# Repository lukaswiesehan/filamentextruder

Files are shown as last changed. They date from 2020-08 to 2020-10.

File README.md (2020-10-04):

# Filament-Extruder <!-- omit in toc -->

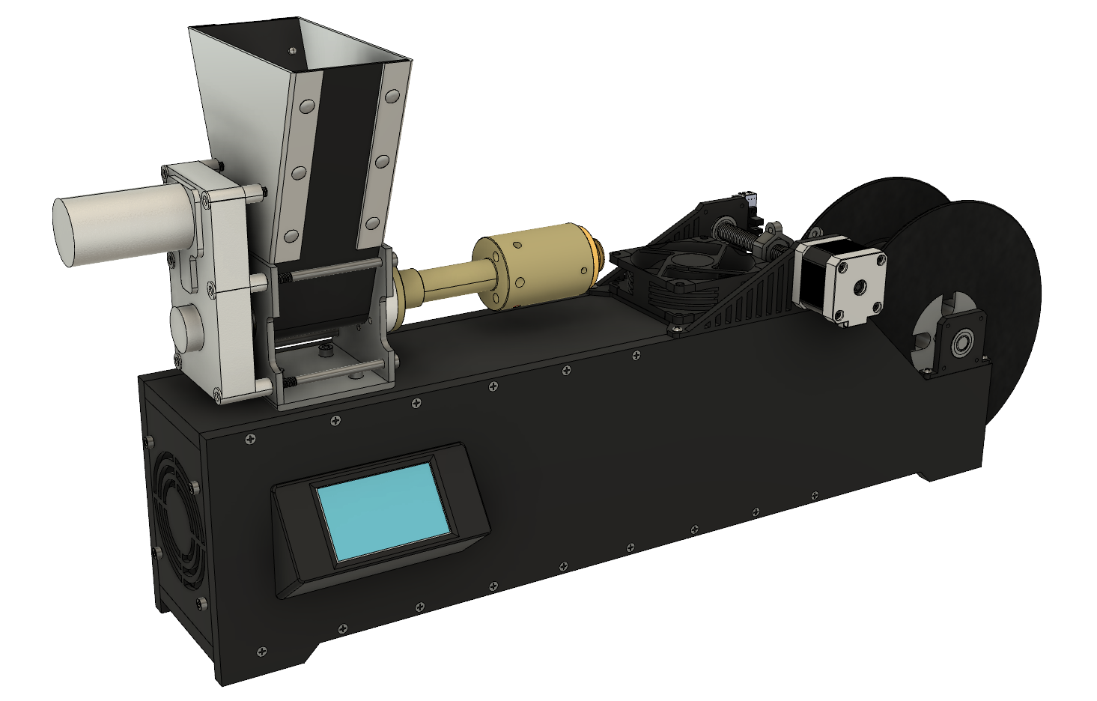
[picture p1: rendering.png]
HMI Preview


Bachelorprojekt im Studiengang Mechatronik, HAW Hamburg.  
*Entwickelt von Tobias Freytag, Anton Neike, Max Sahlke, Lukas Wiesehan.  
Betreut von Prof. Dr. Dietmar Pähler.*

###### Inhalt <!-- omit in toc -->
- [Einführung](#einführung)
- [Repo-Struktur](#repo-struktur)
- [Hardware](#hardware)
  - [Bestellliste](#bestellliste)
  - [Verdrahtung des Systems](#verdrahtung-des-systems)
    - [Arduino Mega](#arduino-mega)
    - [Arduino Nano](#arduino-nano)
    - [Mosfet-Module](#mosfet-module)
    - [Heizpatronen](#heizpatronen)
    - [PT100 Signalverstärker](#pt100-signalverstärker)
    - [PT100 Temperatursensor](#pt100-temperatursensor)
    - [Relais-Modul](#relais-modul)
    - [Extruder Motor](#extruder-motor)
    - [Filament-Lüfter](#filament-lüfter)
    - [Schrittmotortreiber](#schrittmotortreiber)
    - [Schrittmotoren](#schrittmotoren)
    - [Optischer Endschalter](#optischer-endschalter)
- [Software](#software)
- [Konfiguration des Systems](#konfiguration-des-systems)
- [Bedienung des Systems](#bedienung-des-systems)

## Einführung

Im Rahmen des Bachelorprojekts im 5. Semester des Bachelorstudiengangs Mechatronik an der HAW Hamburg soll eine Anlage konstruiert und realisiert werden, 
die aus Kunststoffgranulat 3D-Druck Filament extrudiert und dieses auf entsprechende Rollen aufspult. Übergeordnetes Ziel ist es, Prototypen oder 
fehlgeschlagene Druckteile zu schreddern, um sie erneut zu Filament zu extrudieren und dieses erneut zu verwenden. Da sowohl die Qualität des Kunststoffs, als
auch die Verarbeitbarkeit unter häufigem Aufschmelzen leiden, soll das mit der Anlage hergestellte Filament lediglich für den Druck von Prototypen verwendet
werden.

###### Funktionsschema <!-- omit in toc -->
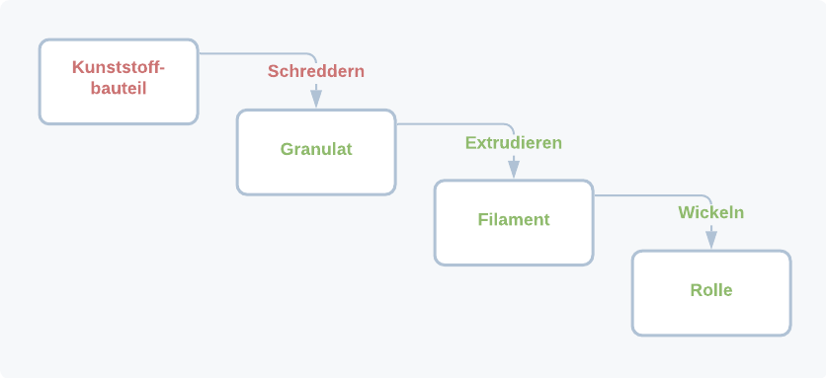
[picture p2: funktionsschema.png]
Funktionsschema


Die im Funktionsschema grün dargestellten Elemente sind Teil dieses Projekts. Die Konstruktion eines Schredders ist im Rahmen dieses Projekts nicht möglich, allerdings
kann das System in Folgeprojekten durchaus mit einem Schredder erweitert werden, der auf den Trichter des Extruders aufgesetzt werden sollte.

## Repo-Struktur

Das Stammverzeichnis des Repositorys beinhaltet alles, was für eine Rekonstruktion des Systems notwendig ist. Es teilt sich in folgende Unterverzeichnisse auf.

| Verzeichnis | Inhalt |
|---|---|
| [`/arduino`](/arduino) | Arduino-Projekte, Liste der notwendigen Libraries, Anleitung zur notwendigen Modifikation der Nextion-Library |
| [`/cad`](/cad) | CAD-Modell des fertigen Systems, `.stl`-Dateien der gedruckten Einzelteile |
| [`/hmi`](/hmi) | `.HMI`-Datei und Anleitung zur Installation des Interfaces auf dem Nextion Display, Screenshots des Interfaces |

Die hier abgelegten Daten entsprechen dem finalen Entwicklungsstand des Systems. Die **ausführliche Projektdokumentation**, in der die einzelnen Entwicklungsschritte 
während des Projekts näher ausgeführt sind, ist als [Wiki dieses Repos](https://github.com/lukaswiesehan/filamentextruder/wiki) realisiert.

## Hardware

Nachfolgend werden alle Komponenten aufgelistet, die bestellt werden müssen. Gehäuse- und Druckteile sind in [`/cad`](/cad) abgelegt und können auf unterschiedliche Weise gefertigt 
werden, weshalb sie in der Kostenaufstellung nicht berücksichtigt werden. Zudem werden Kabel zur Verdrahtung des Systems benötigt, die hier ebenfalls nicht aufgelistet sind.

### Bestellliste

| Anzahl | Bezeichnung | Beschreibung | Preis |
|:---:| --- | --- |:---:|
| 1x | [Felfil Evo Basic Kit](https://felfil.com/shop/felfil-evo-basic-kit/?v=5ea34fa833a1) | Basiskomponenten des Extruders als Bausatz | 299,00€ |
| 1x | [Kaltgerätebuchse](https://www.amazon.de/Hifi-Lab-Einbau-Stecker-Einbau-Buchse-Kaltger%C3%A4te-Buchse/dp/B01H5MK3OI) | Spannungsversorgung des Systems | 6,39€ |
| 1x | [Kaltegeräte-Anschlusskabel](https://www.conrad.de/de/p/hawa-1008230-kaltgeraete-anschlusskabel-schwarz-2-00-m-621535.html) | Spannungsversorgung des Systems | 4,86€ |
| 1x | [Netzteil 24V 320W](https://www.conrad.de/de/p/mean-well-rsp-320-24-ac-dc-netzteilbaustein-geschlossen-13-4-a-321-6-w-24-v-dc-1293056.html) | Primäre Spannungsquelle des Systems | 62,38€ |
| 1x | [Spannungswandler XL4016](https://www.az-delivery.de/products/xl4016-step-down-buck-converter-dc-dc?_pos=5&_sid=a325961b4&_ss=r) | Spannungsversorgung der 12V-Komponenten (Extrudermotor & Lüfter) | 8,49€ |
| 1x | [Spannungswandler LM2596S](https://www.az-delivery.de/products/lm2596s-dc-dc-step-down-modul-1?_pos=6&_sid=619fecdd6&_ss=r) | Spannungsversorgung der 5V-Komponenten (Display & Arduino) | 5,29€ |
| 1x | [Arduino Mega](https://www.az-delivery.de/products/mega-2560-r3-board-mit-atmega2560-100-arduino-kompatibel-ohne-usb-kabel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) | Steuerung des Extruder-Systems und des HMI | 13,79€ |
| 1x | [Arduino Nano](https://www.az-delivery.de/products/nano-v3-mit-ch340-arduino-kompatibel) | Steuerung des Wicklungsmechanismus | 6,49€ |
| 1x | [Nextion Display NX4024K032](https://www.amazon.de/MakerHawk-Nextion-NX4024K032-erweiterte-Versionen/dp/B072FN3SFH/) | Anzeige und Touch-Interface zur Steuerung des Systems | 38,44€ |
| 3x | [Mosfet Modul IRF520](https://www.az-delivery.de/products/irf520-mos-driver-modul-0-24v-5a?_pos=1&_sid=0db666f69&_ss=r) | Steuerung der Heizpatronen | 4,29€ |
| 3x | [Heizpatrone 24V](https://www.conrad.de/de/p/24v-40w-heizpatrone-j-head-hotend-heater-cartridge-3d-drucker-802287254.html) | Heizmodule des Extruders | 4,50€ |
| 1x | [Temperatursensor PT100](https://www.conrad.de/de/p/heraeus-nexensos-w-eyk-6-pt100-platin-temperatursensor-40-bis-500-c-100-3850-ppm-k-172412.html) | Sensor zur Bestimmung der Extrudertemperatur | 15,03€ |
| 1x | [Adafruit MAX31865](https://www.conrad.de/de/p/adafruit-pt1000-rtd-temperature-sensor-amplifier-max31865-802235187.html) | Modul zur Wandlung des Sensorsignals des PT100 | 19,33€ |
| 2x | [Schrittmotortreiber SMD356C](https://www.conrad.de/de/p/waveshare-smd356c-three-phase-hybrid-stepper-motor-driver-806805951.html) | Steuerung der Wicklungsmotoren | 41,44€ |
| 2x | [Schrittmotor NEMA-17](https://www.conrad.de/de/p/joy-it-schrittmotor-nema-17-01-nema-17-01-0-4-nm-1-68-a-wellen-durchmesser-5-mm-1597325.html) | Antriebe des Wicklungsmechanismus | 27,20€ |
| 1x | [Optischer Endschalter](https://www.amazon.de/Homyl-Optischer-Begrenzungsschalter-Endanschlag-Werkzeuge-Rot/dp/B07MHFTVNF/) | Referenzierung des Führungsmotors | 2,51€ |
| 1x | [Relais-Modul KY-019](https://www.az-delivery.de/products/relais-modul) | Schalten des Extrudermotors | 4,99€ |
| 2x | [PC-Lüfter 80x80x25](https://www.conrad.de/de/p/logilink-fan101-pc-gehaeuse-luefter-schwarz-b-x-h-x-t-80-x-80-x-25-mm-871001.html) | Kühlung elektronischer Bauteile und des Filaments | 4,18€ |

Die Kosten der elektronischen Bauteile summieren sich damit auf **659,00€** zzgl. diverser Versandkosten sowie der Gehäuse- bzw. Druckteile.
Hierzu zählen Holzschrauben, einige M4- und M5-Schrauben und Muttern, `10 mm` Sperrholz, `2 mm` Aluminiumblech, sowie etwa `250 mm` M12-Gewindestange.

### Verdrahtung des Systems

###### Verdrahtung <!-- omit in toc -->
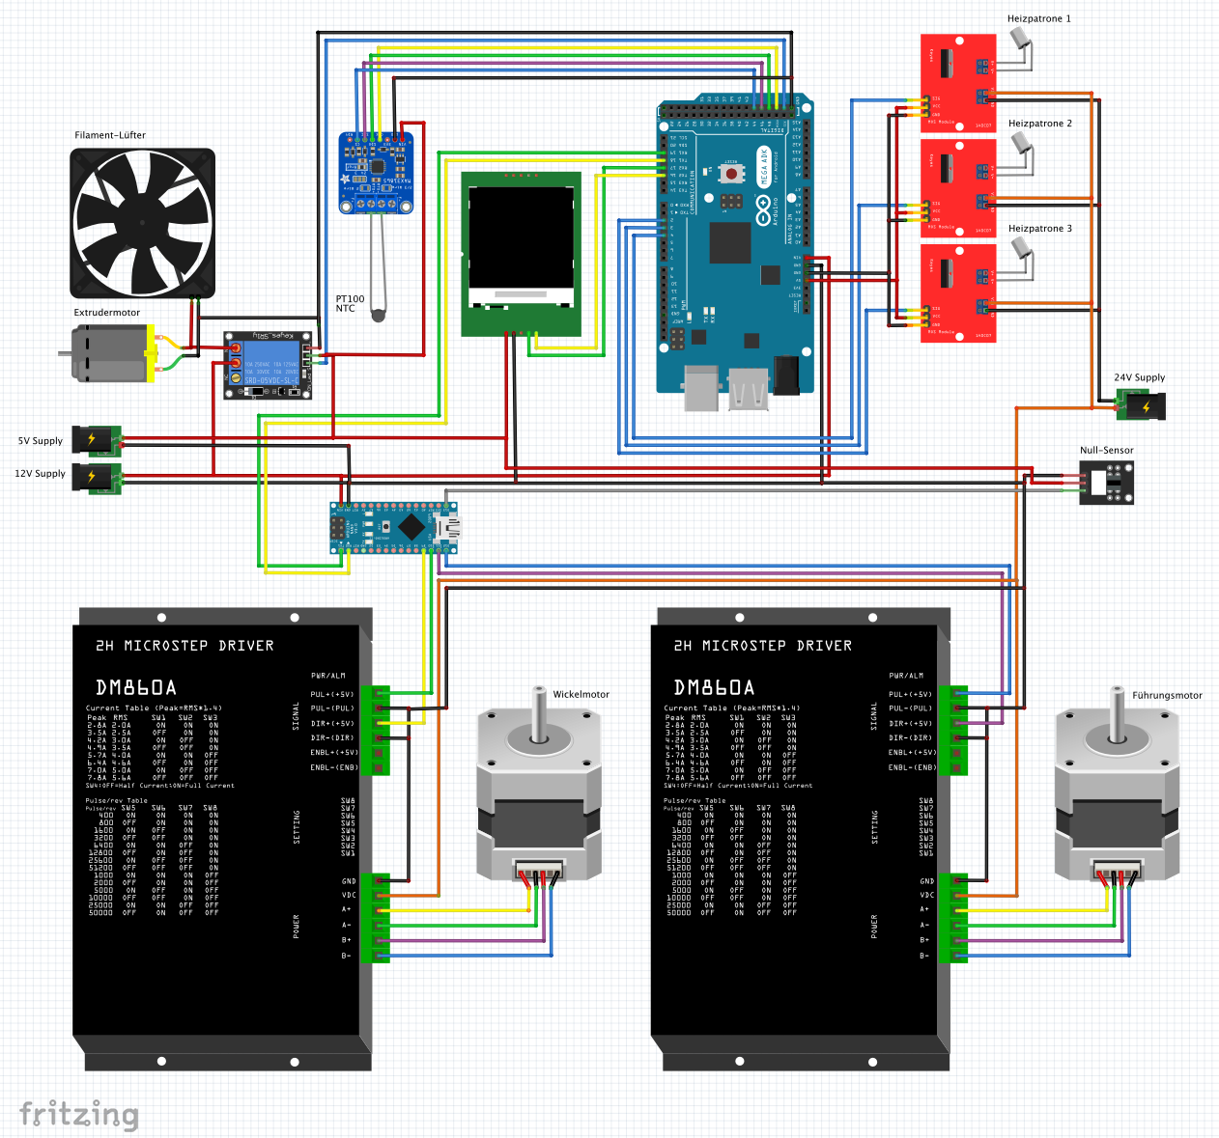
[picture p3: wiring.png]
Verdrahtung


Im oben abgebildeten Schema wurde folgende Farbkonvention eingehalten:
- Schwarz: GND
- Rot: 5-12V VCC
- Orange: 24V VCC
- Blau, Grün, Gelb, Lila: Daten/Signale

*Hinweis: Das Nextion Display wurde im Schema durch ein ähnliches Display ersetzt,
welches sich sowohl im Maßstab, als auch in der Pin-Belegung unterscheidet.*

*Hinweis: Es ist darauf zu achten, dass alle Elemente des Systems auf das selbe `GND`-Niveau gelegt sind.*

#### Arduino Mega

Der Arduino Mega dient als primärer Prozessor des Systems, auf dem die Temperaturregelung
und die Displaysteuerung implementiert sind. Er wird an `GND` und `12 V` Versorgungsspannung angeschlossen.

#### Arduino Nano

Der Arduino Nano wird für die Steuerung des Wicklungsmechanismus benötigt, da die Ansteuerung
der Schrittmotoren eine Signalfrequenz benötigt, die auf dem Mega wegen der darauf laufenden 
Temperaturregelung nicht gewährleistet werden kann. Der Nano wird zur Versorgung ebenfalls
an `GND` und `12 V` angeschlossen. Zudem wird der Hardware-Serial des Nanos mit den Pins `TX`
und `RX` an `RX1` und `TX1` des Mega, also dessen Hardware-Serial 1 verbunden, sodass eine
Kommunikation zwischen den beiden Arduinos implementiert werden kann.

#### Mosfet-Module

Die drei Mosfet-Module werden jeweils `GND` und `24 V` Versorgungsspannung angeschlossen.
Für die Ansteuerung werden `GND` und `VCC` mit dem `5 V` Ausgang und `SIG` mit je einem 
PWM-Ausgang (hier Pins `1`, `2` und `3`) des Arduino Mega verbunden. 

#### Heizpatronen

Die Heizpatronen werden jeweils an die beiden Ausgangs-Terminals der Mosfet-Module angeschlossen. Die Polarität spielt hierbei keine Rolle.

#### PT100 Signalverstärker

Das Adafruit-Modul MAX31865 zum Auslesen des PT100-Sensors wird an `GND` und `5 V` Versogungsspannung angeschlossen. Zur Übertragung der Temperatur an den Arduino Mega werden
die Pins `CS`, `DI`, `DO` und `CLK` an vier Digital-Pins (hier Pins `45`, `47`, `49` und `51`) des Mega angeschlossen.

#### PT100 Temperatursensor

Der PT100 Sensor wird an das Sensorterminal des Adafruit MAX31865 angeschlossen. Da es sich
um einen PT100 mit zwei Kabeln handelt, werden die mittleren beiden Anschlüsse des Moduls
verwendet.

Zur Verwendung des Moduls und des PT100 in Kombination mit einer entsprechenden
Arduino-Library findet sich auf der [Adafruit-Website](https://learn.adafruit.com/adafruit-max31865-rtd-pt100-amplifier/arduino-code) ein umfangreiches Tutorial.

#### Relais-Modul

Das Relais-Modul KY-019 soll zur Steuerung des Extruder-Motors verwendet werden, weshalb an 
den `COM`-Port `12 V` Versorgungsspannung angelegt wird. An der Signalseite wird das Modul
mit `GND` und `5 V` versorgt. Der `SIG`-Pin wird an einen Digitalpin (hier Pin `53`) des Arduino Mega angeschlossen. 

#### Extruder Motor

Der Extruder-Motor wird am Negativ-Pol mit `GND` verbunden, während der Positiv-Pol auf den
`NO`-, also "Normally Open"-Ausgang des Relais-Moduls gelegt wird.

#### Filament-Lüfter

Da der Lüfter zur Kühlung des Filaments nur benötigt wird, sofern extrudiert wird, wird er
analog zum Extruder-Motor mit `GND` versorgt und mit dem Positiv-Pol an das `NO`-Terminal
des Relais-Moduls angeschlossen.

#### Schrittmotortreiber

Die Schrittmotortreiber werden jeweils mit `GND` und `24 V` versorgt. Die `GND`-Leitung kann zudem jeweils direkt mit auf `PUL-` und `DIR-` der Signalterminals gelegt werden. `PUL+` und
`DIR+` werden an jeweils einen Digitalpin des Arduino Nano angeschlossen. Der Wicklungsmotor
ist hier an `10` und `9`, der Führungsmotor an `12` und `11` angeschlossen.

*Wichtig: die Schrittmotortreiber müssen mit den 6 Schaltern auf folgende Konfiguration eingestellt werden.*

| S1 | S2 | S3 | S4 | S5 | S6 |
|:-:|:-:|:-:|:-:|:-:|:-:|
| 0 | 0 | 0 | 1 | 1 | 0 |

#### Schrittmotoren

Die Schrittmotoren werden jeweils an `A-`, `A+`, `B-` und `B+` der Motortreiber angeschlossen. Die genaue Belegung kann vom Schrittmotor abhängig sein, daher wird an 
dieser Stelle auf [dieses Tutorial](https://www.makerguides.com/tb6600-stepper-motor-driver-arduino-tutorial/) verwiesen, in dem beschrieben wird, wie die
die korrekte Belegung der Schrittmotoren bestimmt werden kann.

#### Optischer Endschalter

Der optische Endschalter wird an `GND` und `5 V` Versorgungsspannung angeschlossen und mit
dem `S`- bzw. Signal-Pin auf einen Digitalpin (hier Pin `13`) des Arduino Nano gelegt.

## Software

Die Software besteht aus zwei Komponenten, die sich im Ordner [`/arduino`](/arduino) befinden.
Die genauen Funktionsweisen der Codes können den zugehörigen README-Dateien entnommen werden. 
Wie im Bereich *Hardware* bereits angedeutet, wird das Arduino-Projekt [`filamentextruder`](/arduino/filamentextruder) auf den Arduino Mega und das Projekt [`motorsteuerung`](/arduino/motorsteuerung) auf den Arduino Nano hochgeladen.

Weiterhin muss die Display-Software auf das Nextion-Display geladen werden. Eine kurze Beschreibung dessen findet
sich im Verzeichnis [`/hmi`](/hmi).

## Konfiguration des Systems

Um einen optimalen Prozess zu gewährleisten, sollten vor Inbetriebnahme einige Dinge beachtet werden.

Je nach thermischer Isolation des Extruders werden sich die Reglerparameter ein wenig unterscheiden. Da das System verhältnismäßig träge ist,
stellt das kein großes Problem dar. Um den Aufheizvorgang dennoch hinsichtlich seiner Dauer und Genauigkeit zu optimieren, sollten die PID-Parameter
dem System entsprechend eingestellt werden. Wie dazu vorgegangen werden sollte, kann dem Wiki-Kapitel [Entwicklung/Temperaturregelung](https://github.com/lukaswiesehan/filamentextruder/wiki/Entwicklung#temperaturregelung) entnommen werden. Die bestimmten Reglerparameter können dann in [`filamentextruder.ino`](/arduino/filamentextruder/filamentextruder.ino#L40) aktualisiert werden.

Weiterhin sollte die Basis-Geschwindigkeit der Wicklung an den Extruder angepasst werden, obwohl sie durch die Verwendung des selben mitgelieferten Motors
nur unwesentlich unterscheiden sollte. Im Wiki-Kapitel [Entwicklung/Wicklungsmechanismus](https://github.com/lukaswiesehan/filamentextruder/wiki/Entwicklung#wicklungsmechanismus)
wird ausführlich beschrieben, wie der Parameter `EXTRUSION_FEED` an das System angepasst werden sollte, um einen optimalen Filamentdurchmesser nach der Extrusion
zu gewährleisten. Dieser Parameter wird anschließend in [`motorsteuerung.ino`](/arduino/motorsteuerung/motorsteuerung.ino#L11) aktualisiert.

## Bedienung des Systems

###### Extruder im Prozess <!-- omit in toc -->
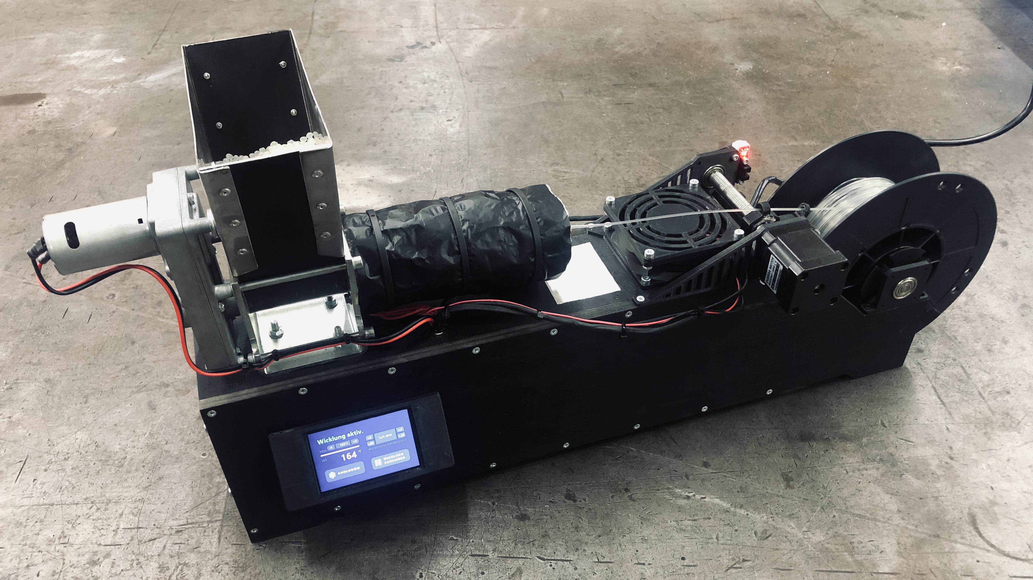
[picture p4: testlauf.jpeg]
Testlauf


Die Benutzeroberfläche wurde mit einer einfachen Bedienbarkeit im Hinterkopf designed. Der Bediener wird im Wesentlichen durch die Seiten geleitet, 
die den verschiedenen States des [Zustandsautomaten](/arduino/filamentextruder#finite-state-machine) entsprechen. Der Ablauf der Bedienung, die 
demnach streng an den Prozess gebunden ist, ist im Folgenden kurz beschrieben.

| Pos. | Beschreibung | Abbildung |
| :-: | --- | --- |
| **1.** | Einschalten der Anlage am Schalter der Kaltgerätebuchse | |
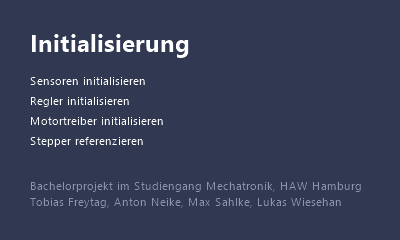
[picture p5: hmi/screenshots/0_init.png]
Initialisierung
| **2.** | Warten, bis das System initialisiert und der Führungsmotor referenziert ist. |  |
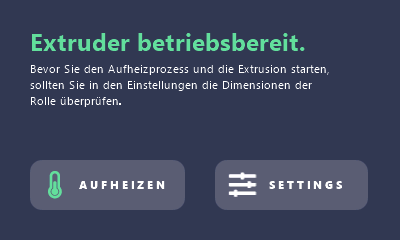
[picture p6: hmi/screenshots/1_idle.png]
Idle
| **3.** | Im Idle-Zustand kann der Bediener entweder den Prozess starten oder die Einstellungen öffnen. |  |
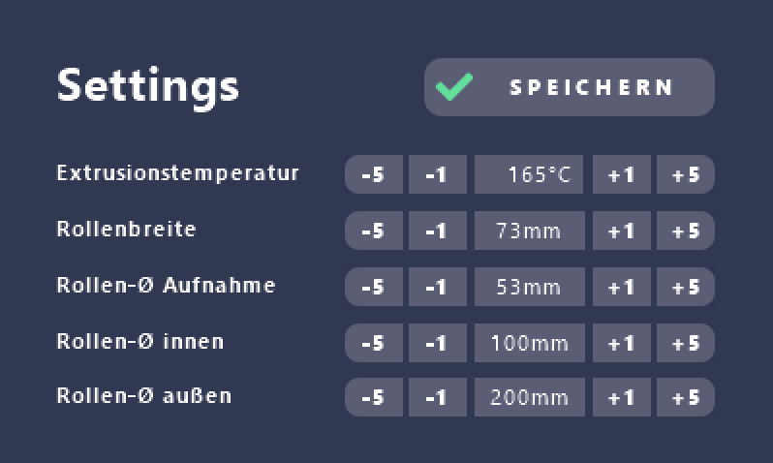
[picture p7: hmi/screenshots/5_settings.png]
Settings
| **3a.** | In den Einstellungen kann die Größe der Spule eingestellt werden, die für den Wicklungsprozess benötigt wird. Außerdem kann die Extrusionstemperatur an den verwendeten Kunststoff angepasst werden. |  |
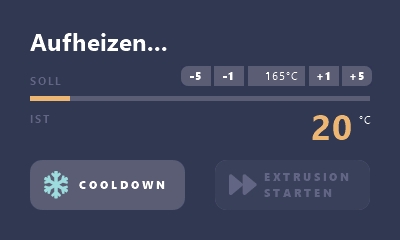
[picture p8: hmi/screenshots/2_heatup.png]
Heatup
| **3b.** | Wählt der Bediener in **3.** den Punkt aufheiten, so wird der Prozess gestartet. Warten, bis die Extrusionstemperatur erreicht ist. Die Extrusionstemperatur kann über die entsprechenden Schaltflächen angepasst werden. |  | 
| **4.** | Extrusion starten, sobald die Extrusionstemperatur erreicht ist. | |
| **5.** | Sobald ausreichend Kunststoff extrudiert ist, den Strang in den Positionierer und anschließend in die Spule einfädeln. | |
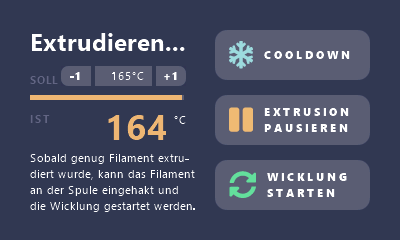
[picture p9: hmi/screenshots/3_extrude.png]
Extrude
| **6.** | Wicklung starten, sobald der Filamentstrang eingefädelt und ein wenig auf Spannung ist. |  |
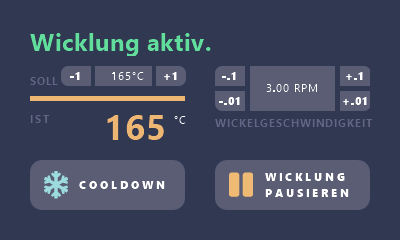
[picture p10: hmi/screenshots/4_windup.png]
Windup
| **7.** | Prozess gelegentlich überprüfen, ggf. Wicklungsgeschwindigkeit über entsprechende Schaltflächen anpassen. |  |
| **8.** | Sobald die Spule ausreichend gefüllt ist, Schaltfläche Cooldown betätigen. | |

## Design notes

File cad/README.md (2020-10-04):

# Konstruktion & CAD <!-- omit in toc -->

###### Inhalt <!-- omit in toc -->
- [Zeichnungen](#zeichnungen)
  - [Gehäuse](#gehäuse)
  - [Einfülltrichter](#einfülltrichter)
- [Druckteile](#druckteile)

## Zeichnungen

### Gehäuse

Das Gehäuse des Systems kann ausschließlich aus `10 mm` starkem Sperrholz hergestellt werden. Die notwendigen
Zeichnungen sind im Verzeichnis [`/zeichnungen`](zeichnungen) abgelegt. Die Gehäusekomponenten sind im folgenden
Rendering schwarz eingefärbt.

###### Rendering des Gesamtsystems <!-- omit in toc -->
Gehäuse

Das Gehäuse besteht im wesentlichen aus vier Platten die zu einem Kasten zusammengeschraubt werden, auf den Extruder
und Wicklungsmechanismus aufgesetzt werden. Die Elektronischen Komponenten können an der Innenseite der Vorderseite
montiert und verkabelt werden. Die linke Seite des Gehäuses, in die der Lüfter eingelassen ist, wird zusätzlich
3D-gedruckt.

| Dokument | Beschreibung |
|---|---|
| [`001_rückseite.pdf`](zeichnungen/001_rückseite.pdf) | Rückseite des Gehäuses mit Aussparung für die Kaltgerätebuchse. An diese Seite wird von innen das Netzteil montiert. |
| [`002_vorderseite.pdf`](zeichnungen/002_vorderseite.pdf) | Vorderseite des Gehäuses mit Aussparung für das Display. An diese Seite werden von innen alle elektronischen Komponenten montiert. |
| [`003_unterseite.pdf`](zeichnungen/003_unterseite.pdf) | Unterseite des Gehäuses. |
| [`004_oberseite.pdf`](zeichnungen/004_oberseite.pdf) | Oberseite des Gehäuses. Auf diese Seite wird der Extruder selbst montiert. |

### Einfülltrichter

Zum Betrieb der Anlage wird außerdem ein Einfülltrichter für das Rohmaterial benötigt, da der Lieferumfang des
Extruder-Bausatzes keinen beinhaltet. Hier wurde ein Trichter konstruiert, der aus `2 mm` starkem Aluminium-Blech
hergestellt werden kann.

###### Einfülltrichter <!-- omit in toc -->
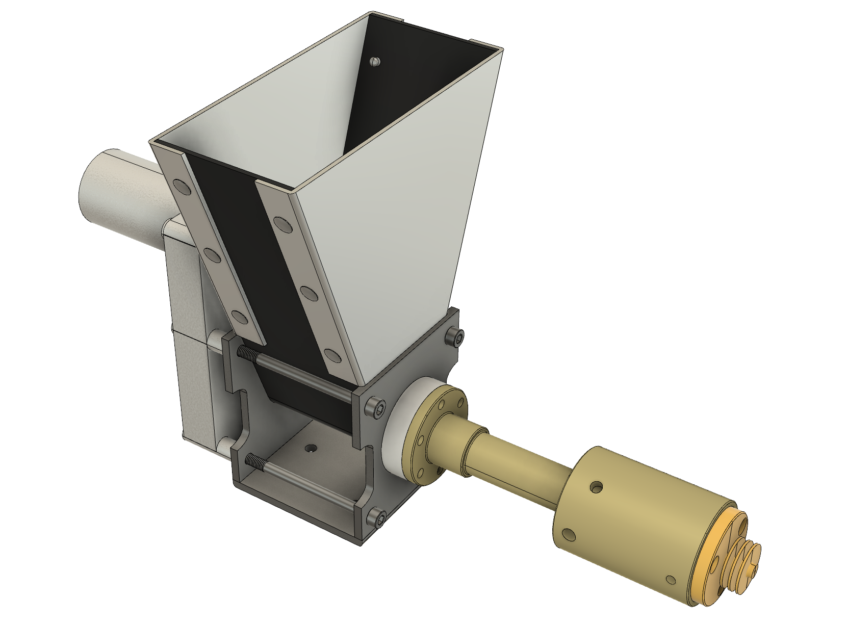
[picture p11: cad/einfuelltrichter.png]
Einfülltrichter


Der Einfülltrichter besteht aus einem Bodenblech und zwei Seitenblechen, die jeweils um 90° abgekantet werden, um
mit dem Bodenblech vernietet zu werden. Eines der Seitenbleche weist zusätzlich zwei Bohrungen auf, an denen der
Trichter am Getriebegehäuse des Extrudermotors fixiert werden kann.

| Dokument | Beschreibung |
|---|---|
| [`005_trichter_seite1.pdf`](zeichnungen/005_trichter_seite1.pdf) | Im Rendering sichtbare Vorderseite des Trichters. |
| [`006_trichter_seite2.pdf`](zeichnungen/006_trichter_seite2.pdf) | Rückseite des Trichters. Mit zwei Bohrungen zur Fixierung des Trichters am Getriebegehäse versehen. |
| [`007_trichter_boden.pdf`](zeichnungen/007_trichter_boden.pdf) | Bodenblech des Trichters, das wesentlich für den Einlauf des Rohmaterials zur Schnecke sorgt. |

## Druckteile

Neben Gehäuseteilen und Einfülltrichter werden zum vollständigen Aufbau des Systems einige Druckteile benötigt. 
Diese sind im Wesentlichen im Bereich des Wicklungsmechanismus verbaut. Alle Druckteile sind als `.stl`-Files im
Verzeichnis [`/prints`](prints) abgelegt und der Übersicht halber nachfolgend abgebildet.

| Druckdatei | Abbildung |
|---|---|
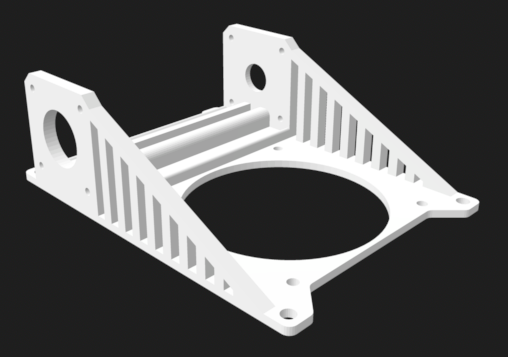
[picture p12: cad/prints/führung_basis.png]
führung_basis.stl
| [`führung_basis.stl`](prints/führung_basis.stl) |  |
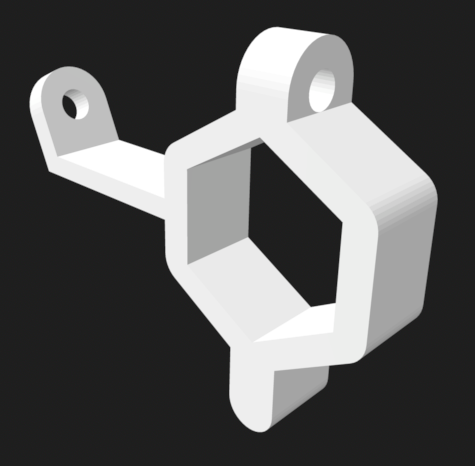
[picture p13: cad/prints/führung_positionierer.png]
führung_positionierer.stl
| [`führung_positionierer.stl`](prints/führung_positionierer.stl) |  |
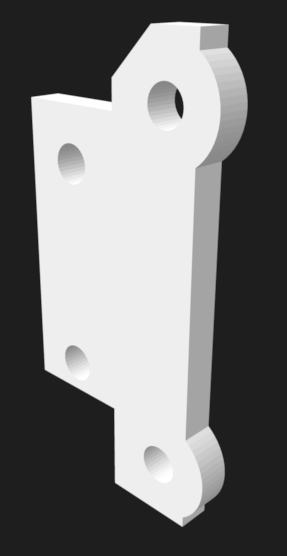
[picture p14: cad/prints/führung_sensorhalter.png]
führung_sensorhalter.stl
| [`führung_sensorhalter.stl`](prints/führung_sensorhalter.stl) |  |
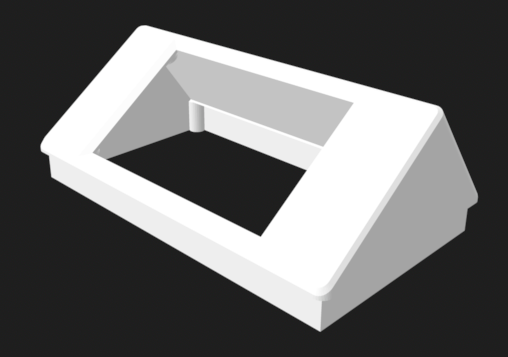
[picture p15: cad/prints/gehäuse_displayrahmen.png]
gehäuse_displayrahmen.stl
| [`gehäuse_displayrahmen.stl`](prints/gehäuse_displayrahmen.stl) |  |
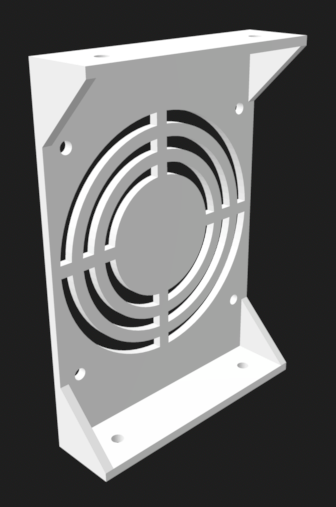
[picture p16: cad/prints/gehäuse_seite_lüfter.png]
gehäuse_seite_lüfter.stl
| [`gehäuse_seite_lüfter.stl`](prints/gehäuse_seite_lüfter.stl) |  |
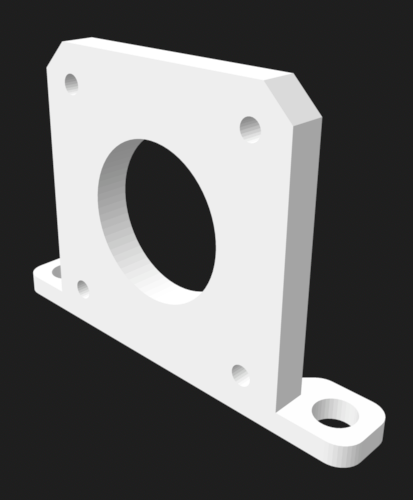
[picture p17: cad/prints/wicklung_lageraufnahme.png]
wicklung_lageraufnahme.stl
| [`wicklung_lageraufnahme.stl`](prints/wicklung_lageraufnahme.stl) |  |
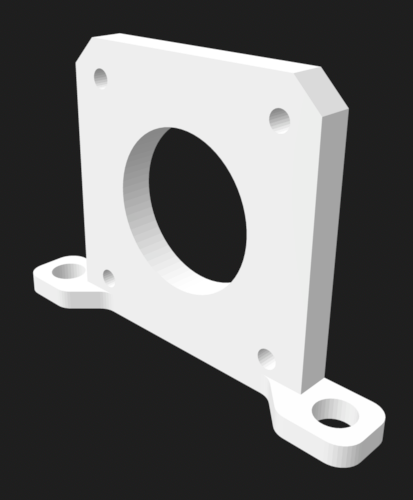
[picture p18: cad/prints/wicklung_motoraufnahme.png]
wicklung_motoraufnahme.stl
| [`wicklung_motoraufnahme.stl`](prints/wicklung_motoraufnahme.stl) |  |
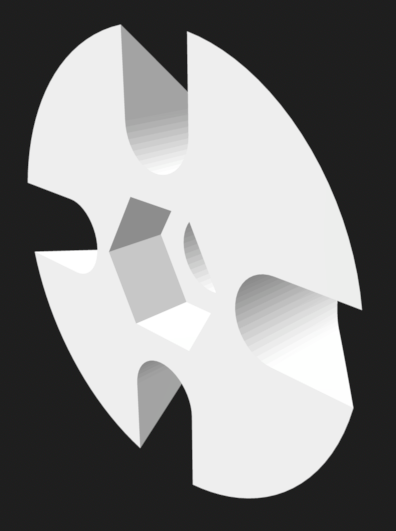
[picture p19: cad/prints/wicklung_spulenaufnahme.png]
wicklung_spulenaufnahme.stl
| [`wicklung_spulenaufnahme.stl`](prints/wicklung_spulenaufnahme.stl) |  |

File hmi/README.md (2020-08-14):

# Human Machine Interface <!-- omit in toc -->

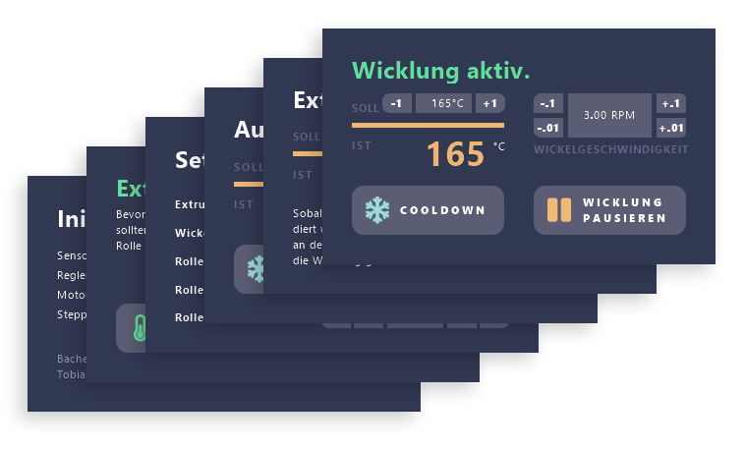
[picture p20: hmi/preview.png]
HMI Preview


Das Interface läuft auf einem [Nextion NX4024K032](https://nextion.tech/datasheets/nx4024k032/) Display und wurde mit dem
[Nextion Editor](https://nextion.tech/nextion-editor/#_section1) für Windows erstellt. Es besteht aus 6 Seiten, die im 
Wesentlichen den States der [FSM in der Steuerung](https://github.com/lukaswiesehan/filamentextruder/tree/master/arduino/filamentextruder#finite-state-machine) 
entsprechen. In [`/screenshots`](https://github.com/lukaswiesehan/filamentextruder/tree/master/hmi/screenshots) können die einzelnen
Seiten angeschaut werden.

- [Display Setup](#display-setup)
- [Font Awesome Icons](#font-awesome-icons)

## Display Setup

- Um das HMI-Programm auf das Display zu übertragen wird der [Nextion Editor](https://nextion.tech/nextion-editor/#_section1) benötigt. 
- Das Display muss per USB an den Computer angeschlossen werden, wofür ein [USB-TTL-Converter](https://www.az-delivery.de/products/ftdi-adapter-ft232rl?_pos=1&_sid=0be74c2ba&_ss=r) benötigt wird.
- Die [`extruder.HMI`](/hmi/extruder.HMI)-Datei wird im Nextion Editor geöffnet.
- Im Nextion Editor wird das Programm über den Upload-Button in der Werkzeugleiste auf das Display übertragen.
- Fertig!

## Font Awesome Icons

Alle im Interface verwendeten Icons stammen aus dem kostenlosen Symbolsatz von [Font Awesome](https://fontawesome.com/). Sie wurden
über die entsprechenden `.otf`-Dateien eingebunden, die unter [SIL OFL 1.1](https://scripts.sil.org/cms/scripts/page.php?site_id=nrsi&id=OFL) lizensiert sind.

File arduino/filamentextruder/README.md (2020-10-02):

# Arduino-Code: Filament-Extruder <!-- omit in toc -->

Die Steuerung des Systems ist als *Finite State Machine* umgesetzt und läuft auf einem Arduino Mega.
Die Temperaturregelung des Extruders erfolgt mithilfe eines Software-PID-Reglers, der die Leistung der Heizpatronen über Mosfets
steuern kann, welche per PWM-Signal angesprochen werden.

###### Inhalt <!-- omit in toc -->
- [Finite State Machine](#finite-state-machine)
- [Benötigte Libraries](#benötigte-libraries)
- [Nextion Library Setup](#nextion-library-setup)
  - [Komponenten ein-/ausblenden](#komponenten-ein-ausblenden)
  - [Text bearbeiten](#text-bearbeiten)

## Finite State Machine

Die State Machine, die als Basis der Steuerung dient, kann wie folgt vereinfacht dargestellt werden. 

###### Finite State Machine <!-- omit in toc -->
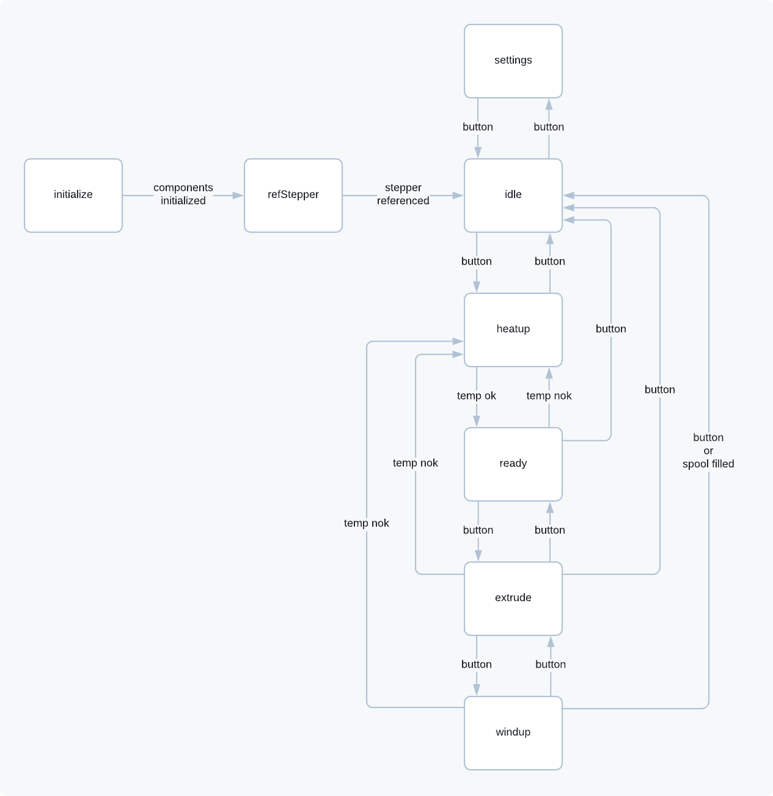
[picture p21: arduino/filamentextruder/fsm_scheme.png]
Finite State Machine


## Benötigte Libraries

- [Nextion.h](https://github.com/itead/ITEADLIB_Arduino_Nextion)
- [Adafruit_MAX31865.h](https://github.com/adafruit/Adafruit_MAX31865)
- [PID_v1.h](https://github.com/br3ttb/Arduino-PID-Library)

## Nextion Library Setup

Zur einfachen Kommunikation zwischen Display und Arduino wird die offizielle 
[Nextion Library](https://github.com/itead/ITEADLIB_Arduino_Nextion) verwendet.
Für eine fehlerfreie Einbindung in das Projekt sind einige Änderungen an der Bibliothek notwendig, die nachfolgend kurz erläutert werden.

### Komponenten ein-/ausblenden

Der `NexButton`-, `NexText` und der `NexPicture`-Klasse Methoden werden hinzugefügt, die es
ermöglichen, diese Komponenten ein- bzw. auszublenden.

###### NexButton.h erweitern <!-- omit in toc -->
```c++
bool hide();
bool show();
```

###### NexButton.cpp erweitern <!-- omit in toc -->
```c++
bool NexButton::hide()
{
  String cmd;

  cmd += "vis ";
  cmd += getObjName();
  cmd += ",0";
  sendCommand(cmd.c_str());
  return recvRetCommandFinished();
}

bool NexButton::show()
{
  String cmd;

  cmd += "vis ";
  cmd += getObjName();
  cmd += ",1";
  sendCommand(cmd.c_str());
  return recvRetCommandFinished();
}
```

Analog zu den Erweiterungen der `NexButton`-Klasse werden auch die `NexText`- und die `NexPicture`-Klasse erweitert.

### Text bearbeiten

Zudem wird die Methode `NexText.setText()` so verändert, dass zum Senden an das Display keine 
Konvertierung in Char-Arrays mehr vorgenommen werden muss.

###### NexText.h bearbeiten <!-- omit in toc -->
```c++
bool setText(String buffer);   
```

###### NexText.cpp bearbeiten <!-- omit in toc -->
```c++
bool NexText::setText(String buffer)
{
  ...
}
```

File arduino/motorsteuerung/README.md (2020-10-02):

# Arduino-Code: Motorsteuerung <!-- omit in toc -->

Da die Steuerung des Wicklungsmechanismus eine hohe Rechenfrequenz benötigt, wird diese
von der restlichen Steuerung entkoppelt und läuft auf einem Arduino Nano. Der Steuerungsalgorithmus der Wicklung basiert im Wesentlichen auf der [AccelStepper](https://www.airspayce.com/mikem/arduino/AccelStepper/index.html)-Library. 

###### Inhalt <!-- omit in toc -->
- [Funktionsweise des Wicklungsmechanismus](#funktionsweise-des-wicklungsmechanismus)
- [Steuerungsalgoritmus](#steuerungsalgoritmus)
- [Kommunikation mit dem Arduino Mega](#kommunikation-mit-dem-arduino-mega)
- [Benötigte Libraries](#benötigte-libraries)

## Funktionsweise des Wicklungsmechanismus

###### Rendering des Wicklungsmechanismus <!-- omit in toc -->
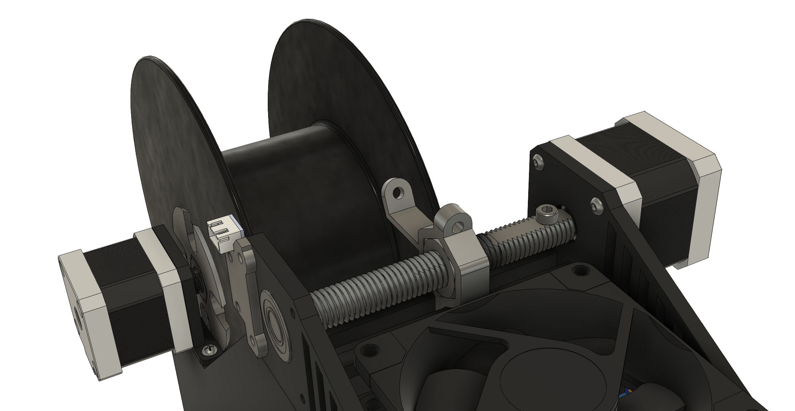
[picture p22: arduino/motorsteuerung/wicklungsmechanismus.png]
Wicklungsmechanismus


Der Kern des Wicklungsmechanismus sind zwei Schrittmotoren. Einer dieser Motoren dreht die Spule, auf die das Filament aufgewickelt werden soll, der andere Motor positioniert das Filament auf der Breite der Spule.

Die Positionierung des Filaments erfolgt über die Rotation einer Gewindestange. Der Positionierer selbst ist mit einer Mutter verklebt, die sich auf der Gewindestange befindet. Die Wahl der Gewindegröße zu `M12` führt dazu, dass die Geschwindigkeiten der
beiden Motoren zu jedem Zeitpunkt gleich sind. Das liegt daran, dass die Steigung des 
Gewindes von `1,75 mm` der Filamentbreite entspricht. So muss der Führungsmotor genau
eine Umdrehung machen, um das Filament zu versetzen, während die Spule ebenfalls genau 
eine Umdrehung macht.

## Steuerungsalgoritmus

Der Ablauf der Steuerung wird im wesentlichen durch die Konstruktion des Wicklungsmechanismus 
bestimmt. Grundsätzlich werden die Motoren lediglich für einige Umdrehungen angesteuert, bevor die 
Rotationsgeschwindigkeit neu berechnet wird, da die Wicklung mit jeder Lage Filament auf der Spule 
verlangsamt werden muss, weil sich der
Wicklungsradius um einen Filamentdurchmesser erhöht.

Der Wicklungsmotor wird also ständig für eine volle Lage Filament, also einige volle Umdrehungen 
angesteuert, wobei die Drehrichtung gleich bleibt.

Der Positionierungsmotor hingegen muss nach jeder Lage Filament nicht nur seine
Drehgeschwindigkeit aktualisieren, sondern auch seine Drehrichtung ändern.

Der sich daraus ergebende Ablauf ist nachfolgend schematisch dargestellt.

###### Schema des Steuerungsalgorithmus <!-- omit in toc -->
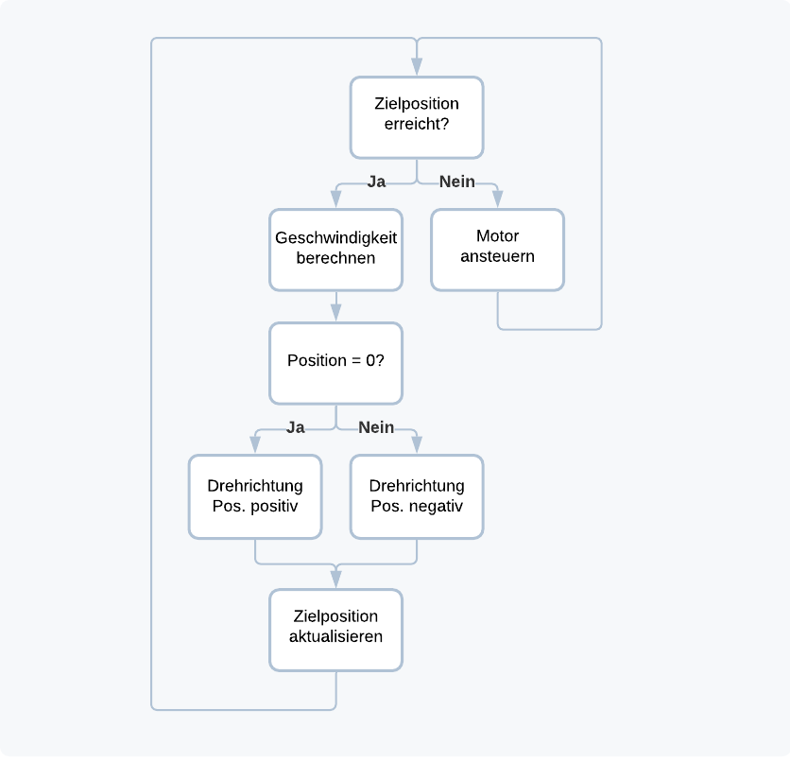
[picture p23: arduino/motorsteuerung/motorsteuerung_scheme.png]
Schema Motorsteuerung


## Kommunikation mit dem Arduino Mega

Da das System einige Einstellungen durch den Bediener ermöglicht, die dementsprechend auf dem Display 
getätigt werden und damit auf dem Arduino Mega gespeichert werden, muss dieser mit dem Arduino Nano
kommunizieren. Die Größe der eingesetzten Spule zur Wicklung des Filaments ist maßgeblich für die 
Steuerung der Motoren. Da Filamentspulen in leicht unterschiedlichen Ausführungen geliefert werden,
können die wesentlichen Abmaße der Spule über das Display angepasst werden. 

Um diese Parameter an den Arduino Nano zu übertragen, bietet sich die serielle Schnittstelle an. Die 
Parameter werden nacheinander in einen String gespeichert und durch ein Semikolon getrennt. So ergibt 
sich ein Muster, welchem jede Nachricht entsprechen muss, die vom Arduino Mega an den Nano gesendet 
wird: `SPOOL_WIDTH;SPOOL_PICKUP_DIAMETER;SPOOL_INNER_DIAMETER;SPOOL_OUTER_DIAMETER;SPEED_OFFSET;`.

Da die aktuelle Wicklungsgeschwindigkeit mithilfe dieser Parametern auf dem Arduino Nano berechnet
wird, aber auf dem Display angezeigt werden soll, muss sie nach jeder Aktualisierung an den 
Arduino Mega zurück gesendet werden. Diese Nachrichten entsprechen folgendem Muster: `WINDUP_SPEED;`.

## Benötigte Libraries

- [AccelStepper.h](https://www.airspayce.com/mikem/arduino/AccelStepper/index.html)

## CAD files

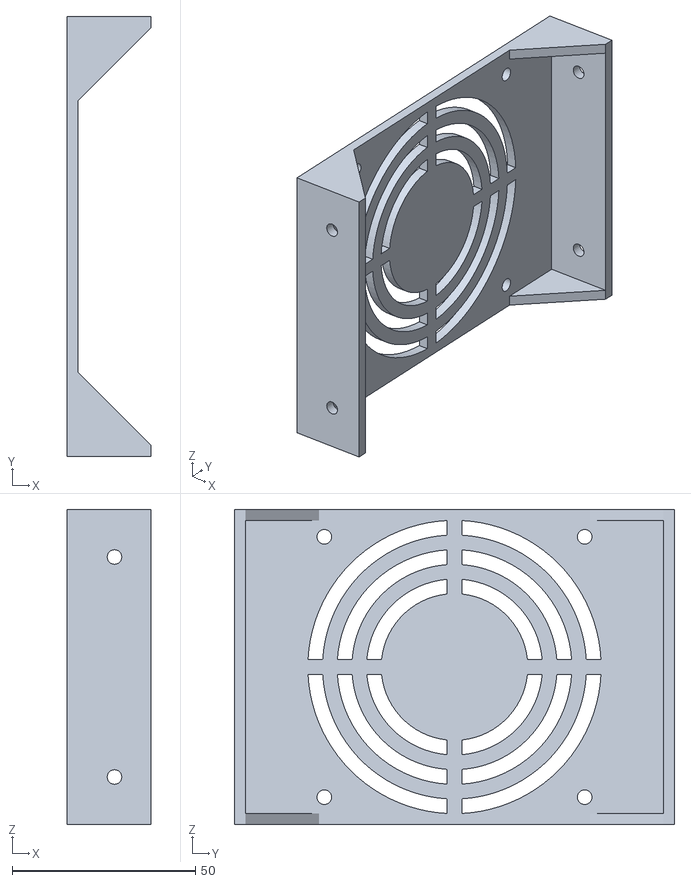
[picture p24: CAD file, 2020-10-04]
cad/prints/gehäuse_seite_lüfter.stl
23.0 x 120.0 x 86.0

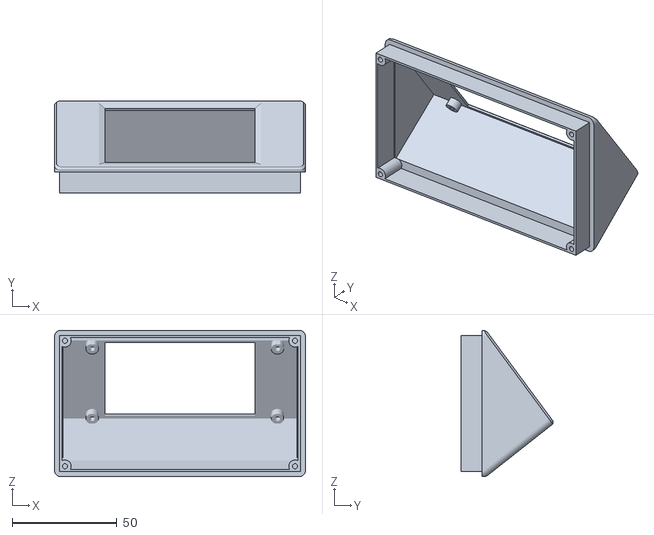
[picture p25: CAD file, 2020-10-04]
cad/prints/gehäuse_displayrahmen.stl
120.0 x 44.1 x 70.0

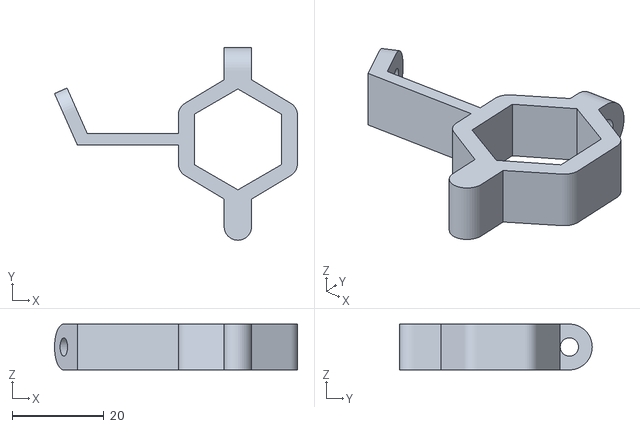
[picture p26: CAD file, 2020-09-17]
cad/prints/führung_positionierer.stl
53.0 x 42.0 x 10.0

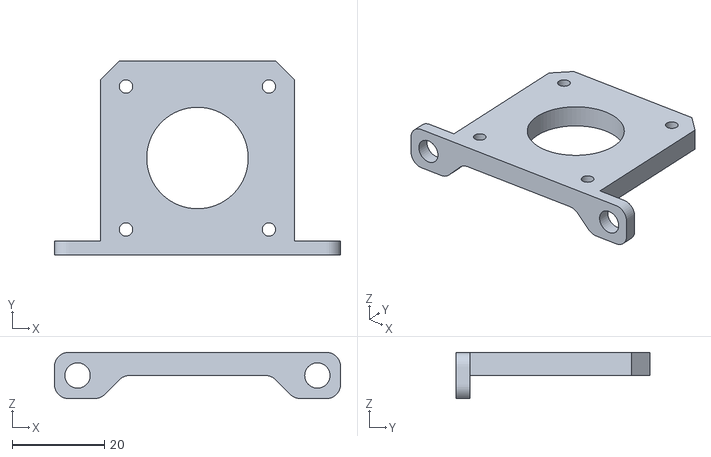
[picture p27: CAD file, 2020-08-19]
cad/prints/wicklung_lageraufnahme.stl
62.0 x 42.0 x 10.0

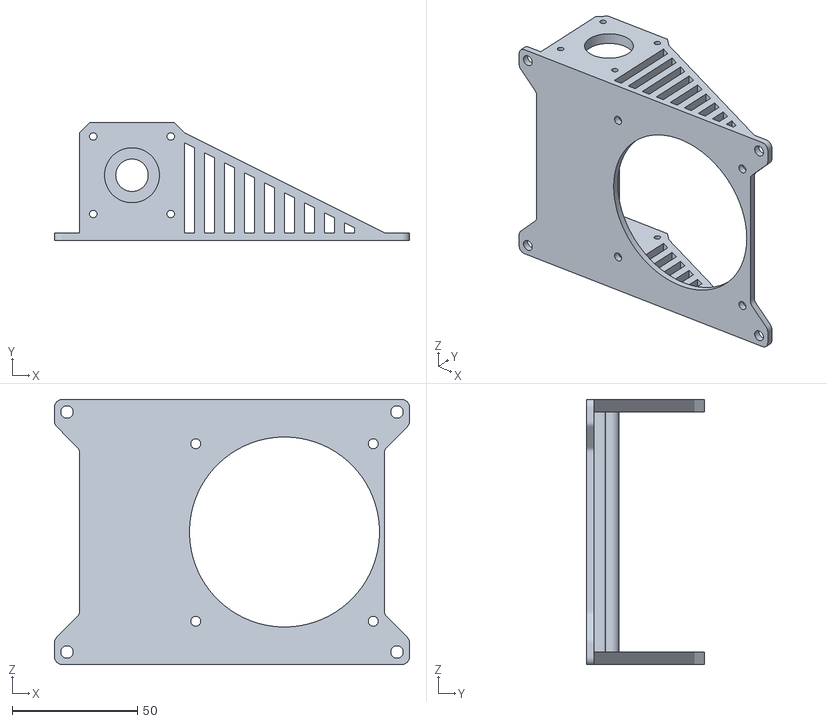
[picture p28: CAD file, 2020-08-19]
cad/prints/führung_basis.stl
142.0 x 47.0 x 106.0

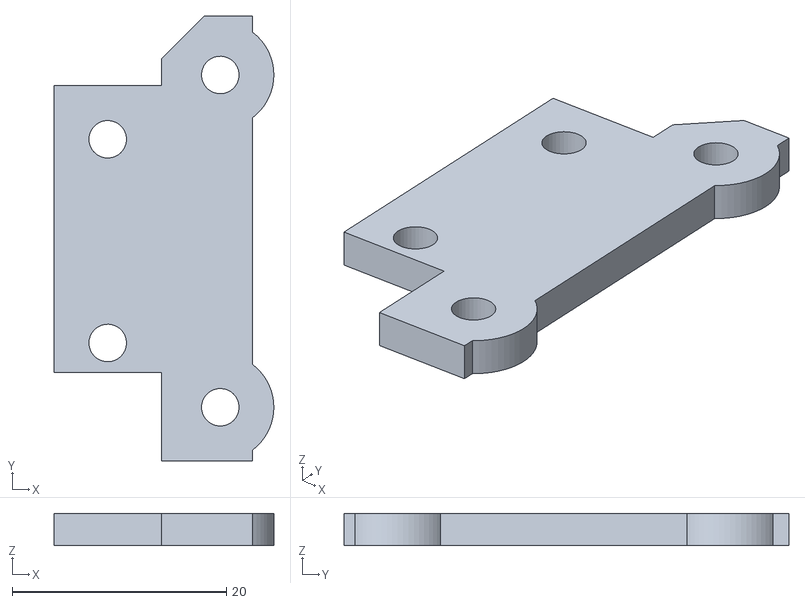
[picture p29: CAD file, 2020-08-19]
cad/prints/führung_sensorhalter.stl
20.5 x 41.5 x 3.00

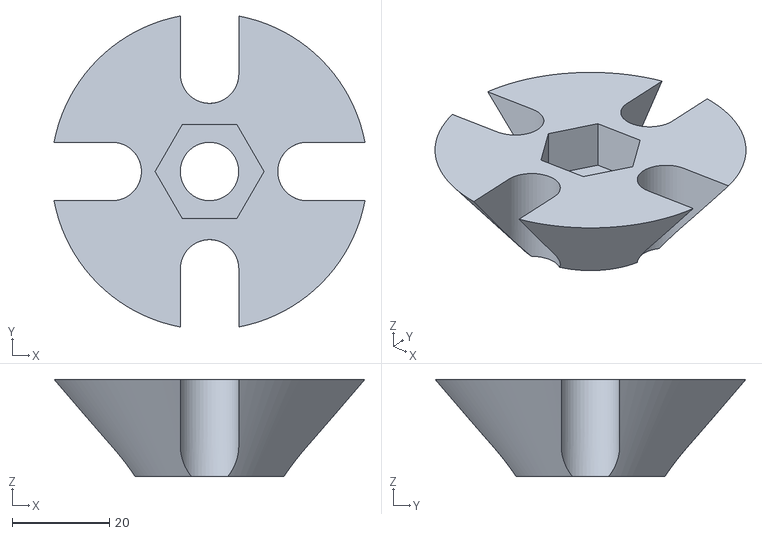
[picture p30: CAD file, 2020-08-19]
cad/prints/wicklung_spulenaufnahme.stl
63.9 x 63.9 x 20.0

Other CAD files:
cad/prints/wicklung_motoraufnahme.stl

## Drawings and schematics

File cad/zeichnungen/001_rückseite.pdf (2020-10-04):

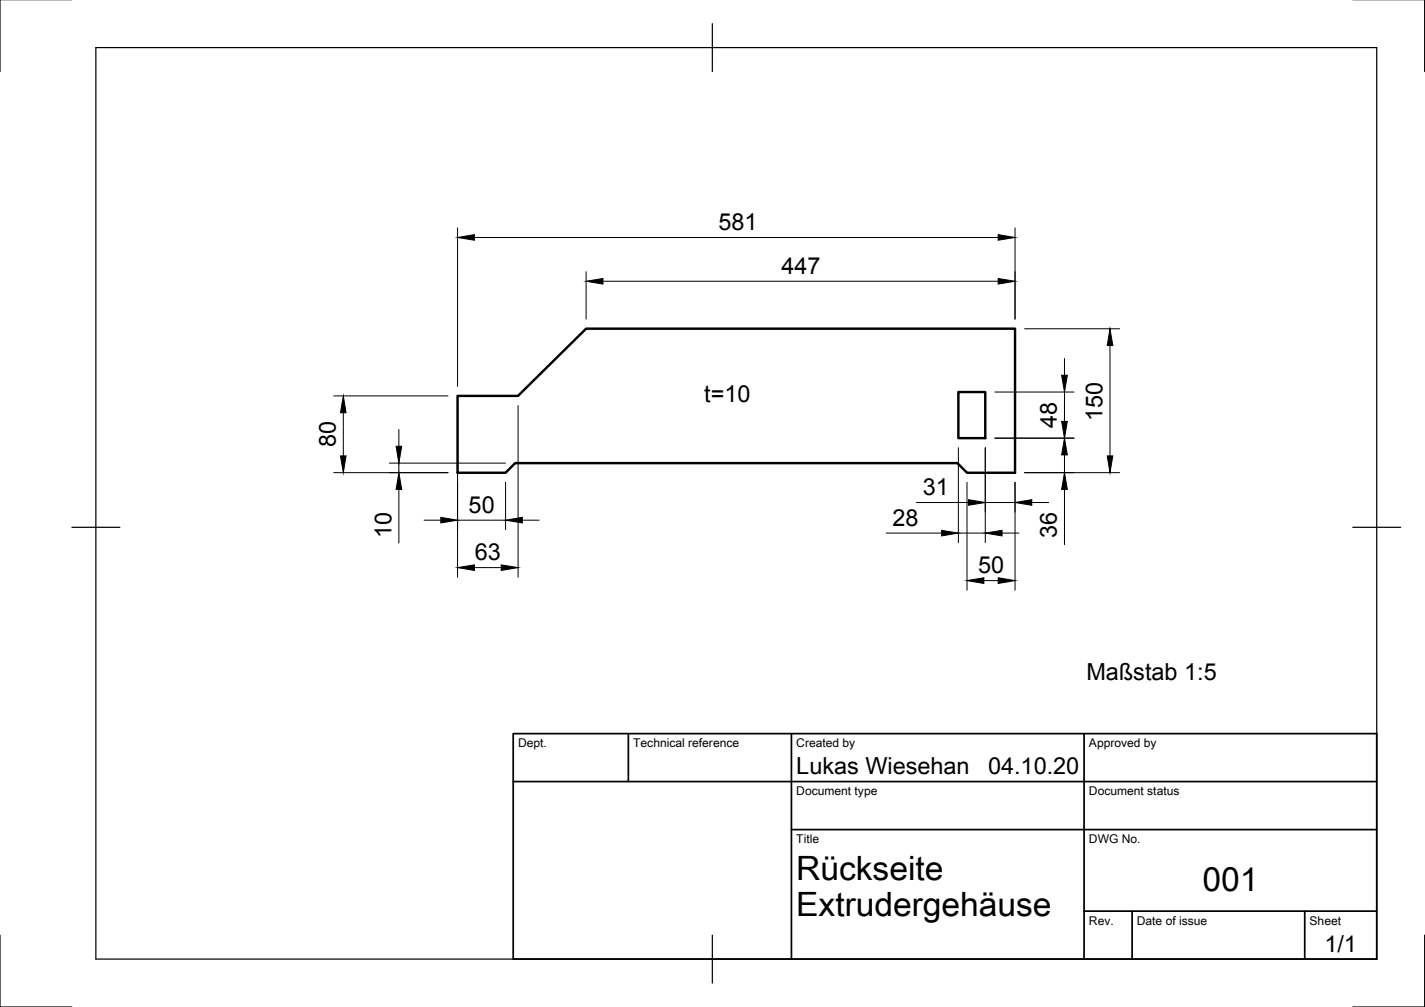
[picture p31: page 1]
Maßstab 1:5

Dept. | Technical reference | Created by Lukas Wiesehan 04.10.20 | Approved by

Document type | Document status

Title Rückseite Extrudergehäuse | DWG No. 001

Rev. | Date of issue | Sheet 1/1

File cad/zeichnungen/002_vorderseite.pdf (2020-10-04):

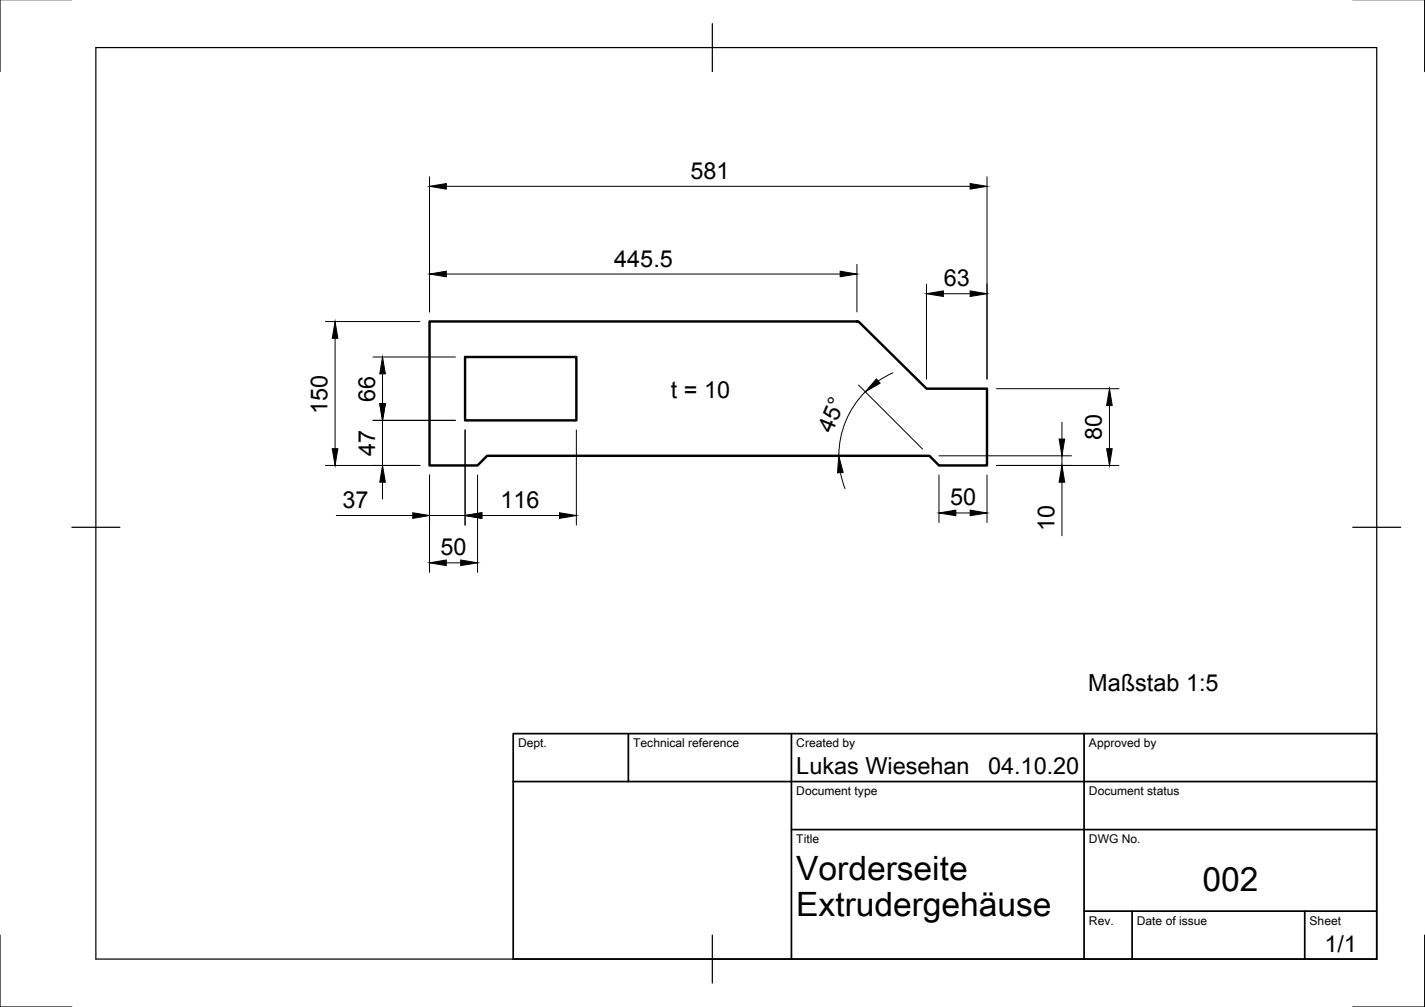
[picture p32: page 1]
Maßstab 1:5

Dept. | Technical reference | Created by Lukas Wiesehan 04.10.20 | Approved by

Document type | Document status

Title Extrudergehäuse | DWG No. 002 Vorderseite

Rev. | Date of issue | Sheet 1/1

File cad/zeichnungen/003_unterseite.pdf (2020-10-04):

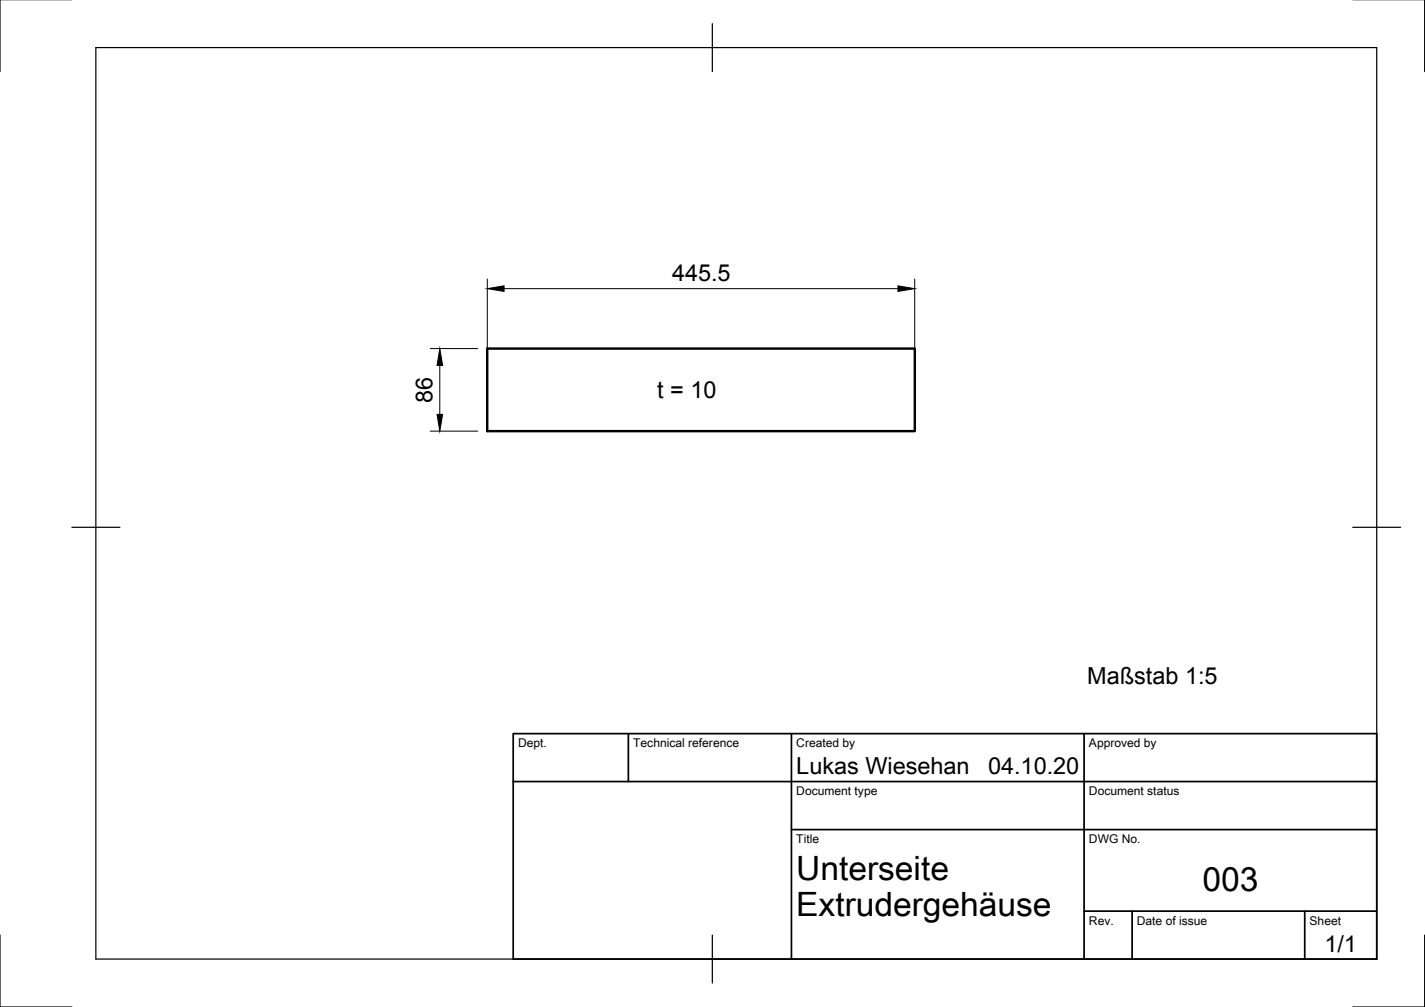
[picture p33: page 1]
Maßstab 1:5 86

Dept. | Technical reference | Created by Lukas Wiesehan 04.10.20 | Approved by

Document type | Document status

Title Unterseite Extrudergehäuse | DWG No. 003

Rev. | Date of issue | Sheet 1/1

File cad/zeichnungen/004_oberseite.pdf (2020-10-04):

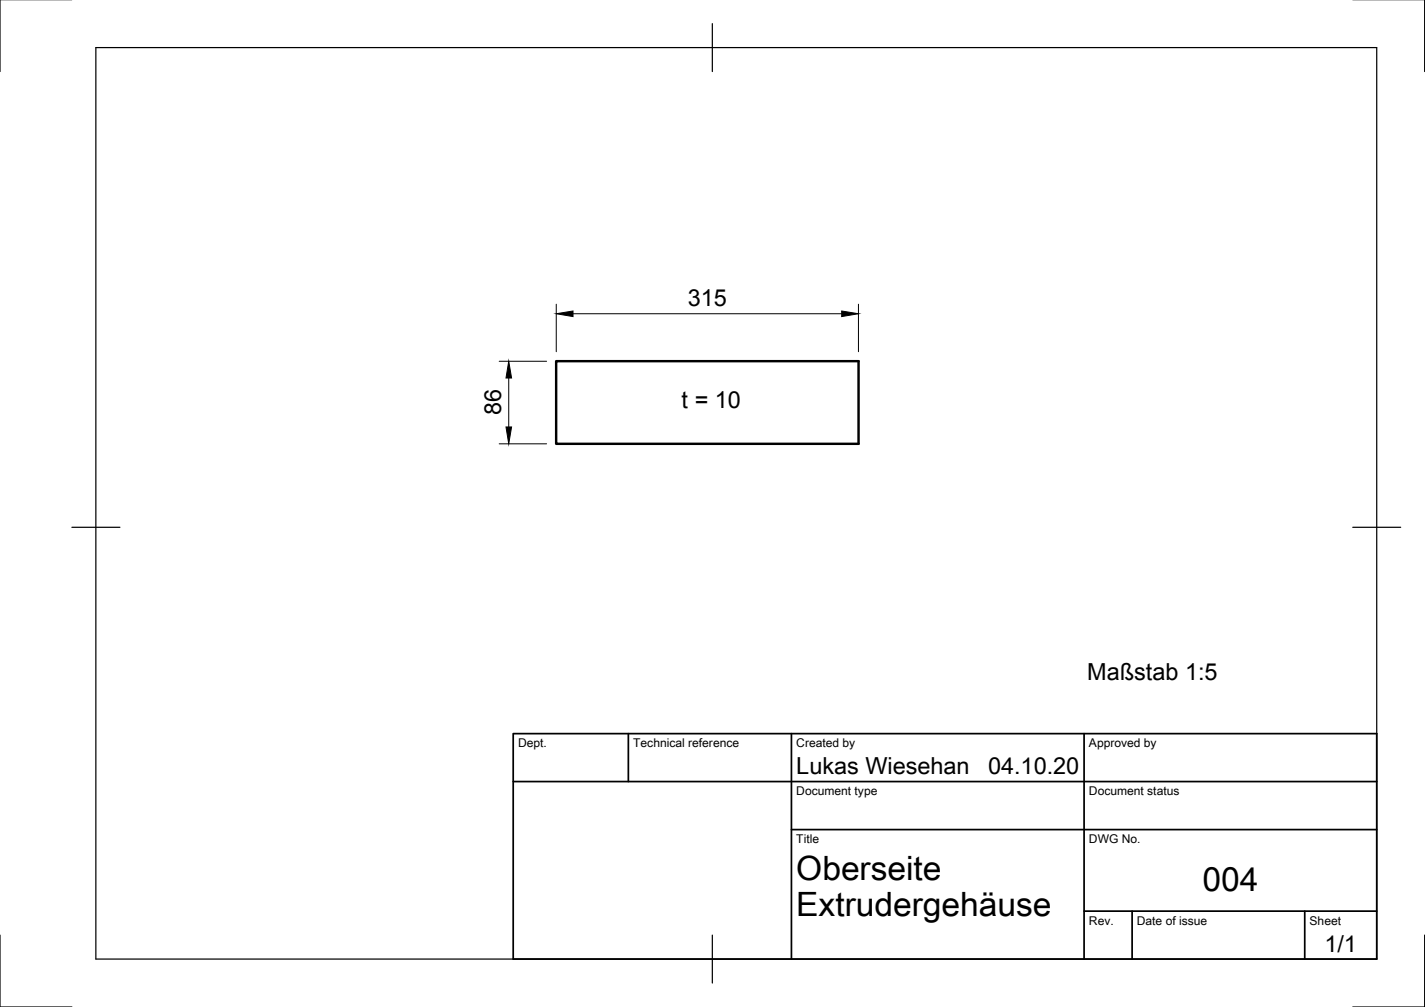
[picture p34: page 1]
Maßstab 1:5 86

Dept. | Technical reference | Created by Lukas Wiesehan 04.10.20 | Approved by

Document type | Document status

Title Oberseite Extrudergehäuse | DWG No. 004

Rev. | Date of issue | Sheet 1/1

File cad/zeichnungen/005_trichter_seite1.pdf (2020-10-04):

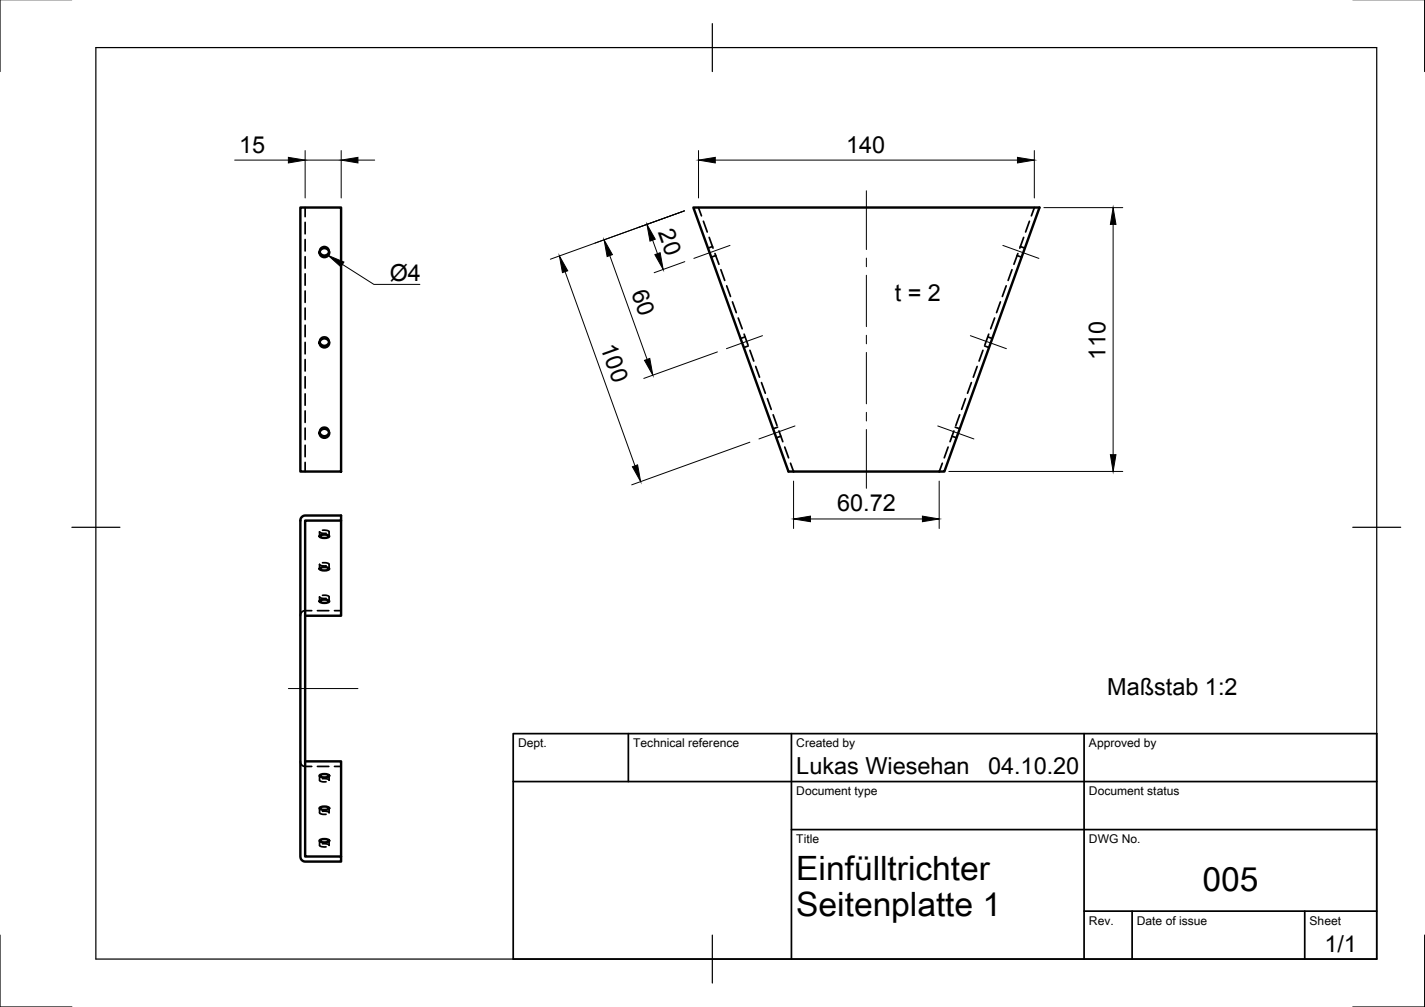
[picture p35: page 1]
Maßstab 1:2

Dept. | Technical reference | Created by Lukas Wiesehan 04.10.20 | Approved by

Document type | Document status

Title Seitenplatte 1 | DWG No. 005 Einfülltrichter

Rev. | Date of issue | Sheet 1/1

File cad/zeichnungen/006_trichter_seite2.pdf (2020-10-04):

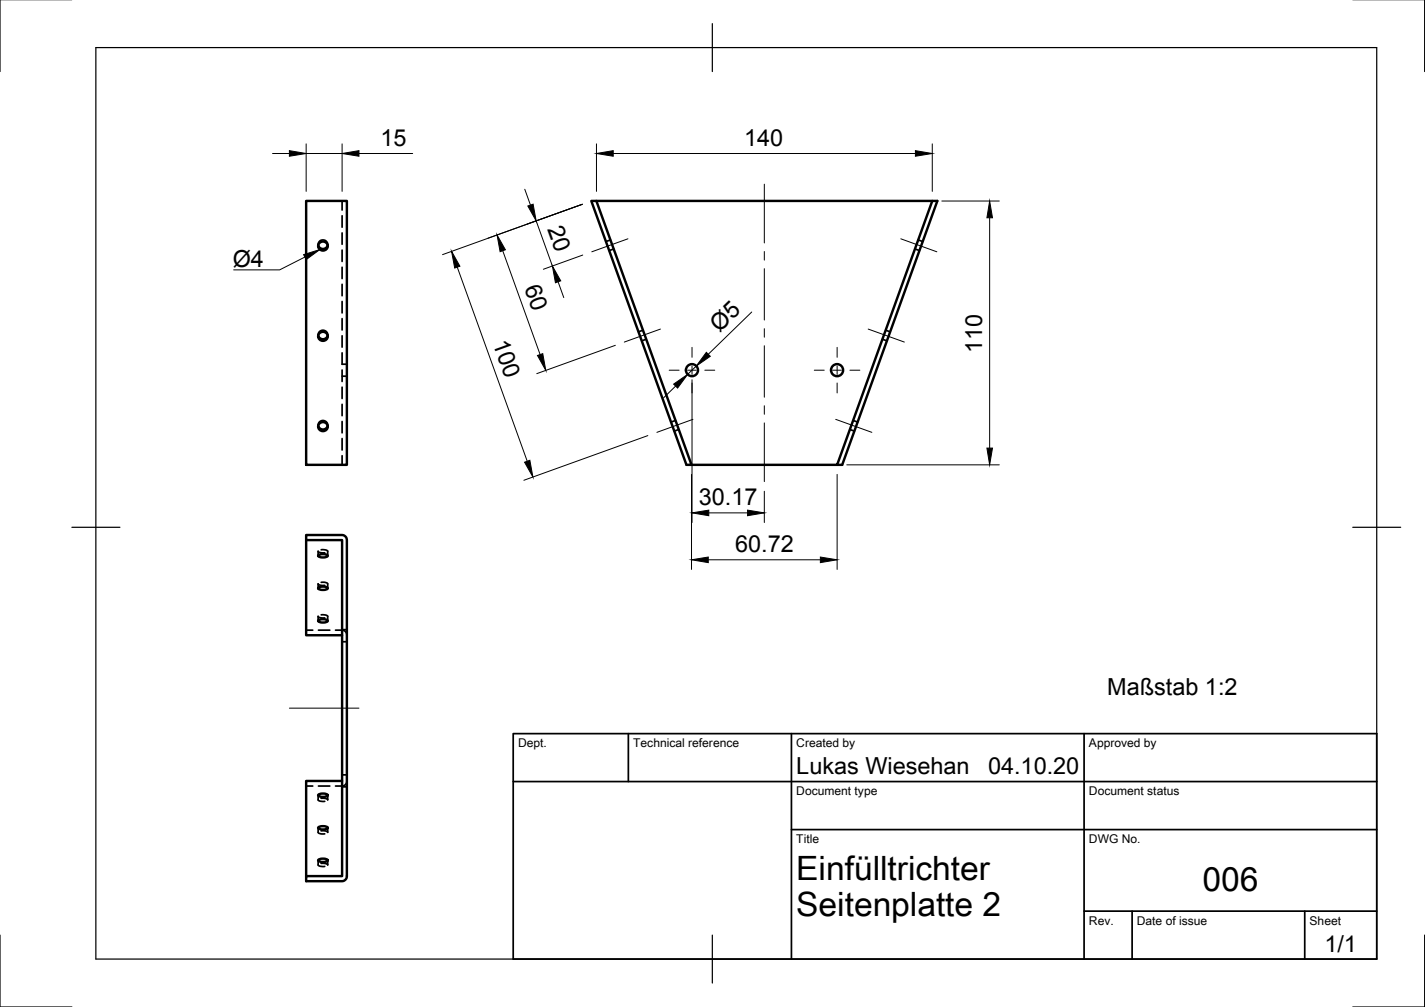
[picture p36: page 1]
Maßstab 1:2

Dept. | Technical reference | Created by Lukas Wiesehan 04.10.20 | Approved by

Document type | Document status

Title Seitenplatte 2 | DWG No. 006 Einfülltrichter

Rev. | Date of issue | Sheet 1/1

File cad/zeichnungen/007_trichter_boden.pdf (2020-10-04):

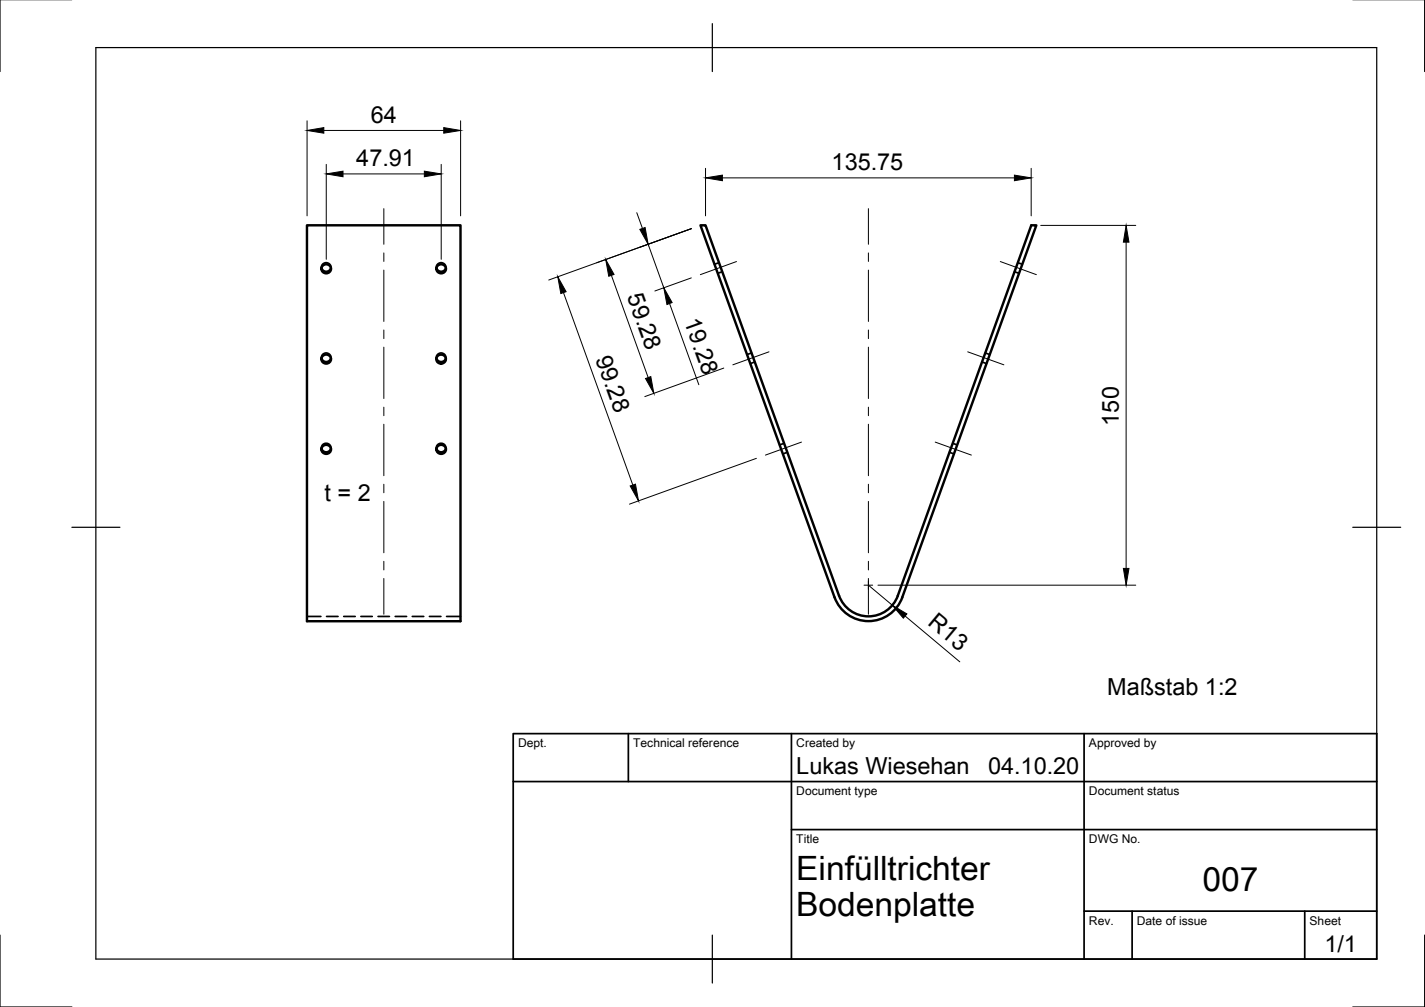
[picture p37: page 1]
Maßstab 1:2

Dept. | Technical reference | Created by Lukas Wiesehan 04.10.20 | Approved by

Document type | Document status

Title Bodenplatte | DWG No. 007 Einfülltrichter

Rev. | Date of issue | Sheet 1/1

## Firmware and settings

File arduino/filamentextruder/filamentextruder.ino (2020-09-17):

//Include libraries
#include "Nextion.h"
#include <Adafruit_MAX31865.h>
#include <PID_v1.h>

//Define defaults
#define NOMINAL_TEMP 165 //[°C]
#define SPOOL_WIDTH 73 //[mm]
#define SPOOL_PICKUP_DIAMETER 53 //[mm]
#define SPOOL_INNER_DIAMETER 100 //[mm]
#define SPOOL_OUTER_DIAMETER 200 //[mm]

//Define other process parameters
#define UPDATE_INTERVAL 1000 //[ms]
#define ALLOWED_TEMP_DEVIATION 5 //[°C]

//Define temperature sensor pins 
#define MAX31865_CS 45 //Any digital pin
#define MAX31865_DI 47 //Any digital pin
#define MAX31865_DO 49 //Any digital pin
#define MAX31865_CLK 51 //Any digital pin  

//Define heater pins
#define HEATER_1 2 //PWM pin
#define HEATER_2 3 //PWM pin
#define HEATER_3 4 //PWM pin

//Define extruder motor pin 
#define EXTRUDER_MOTOR 53 //Any digital pin 

//Define windup signal pins
#define INIT_SIGNAL 5 //Any digital pin
#define REF_SIGNAL 6 //Any digital pin
#define WINDUP_SIGNAL 7 //Any digital pin

//Define PT100 parameters
#define RREF 430.0
#define RNOMINAL 100.0

//Define PID parameters
#define K_P 150.0
#define K_I 1.8
#define K_D 1080.0

//Declare Extruder FSM states
enum states {initialize, refStep, idle, settings, heatup, ready, extrude, windup};
states currentState = initialize;

//Declare extruder process variables
long updateTime = 0L;
double nominalTemp = NOMINAL_TEMP; //[°C]
double actualTemp = 0.0; //[°C]
int spoolWidth = SPOOL_WIDTH; 
int spoolPickupDiameter = SPOOL_PICKUP_DIAMETER;
int spoolInnerDiameter = SPOOL_INNER_DIAMETER;
int spoolOuterDiameter = SPOOL_OUTER_DIAMETER;
int speedOffset = 0; //[1/min]

//Declare temperature sensor 
Adafruit_MAX31865 pt100(MAX31865_CS, MAX31865_DI, MAX31865_DO, MAX31865_CLK);

//Declare PID output variable
double heaterOutput;
PID pid(&actualTemp, &heaterOutput, &nominalTemp, K_P, K_I, K_D, DIRECT);

//Declare stepper motors and corresponding variables
double windupSpeed = 0.0; //[1/min]
int turnsPerLayer = 0;
int stepsPerSecond = 0; //[1/s]
int currentLayer = -1;

//Declare Nextion objects
//Page 0: init
NexPage initPage(0, 0, "init");
NexPicture init_pInitSensors(0, 6, "pInitSensors");
NexPicture init_pInitPID(0, 7, "pInitPID");
NexPicture init_pInitMotors(0, 8, "pInitMotors");
NexPicture init_pRefStepper(0, 9, "pRefStepper");
//Page 1: idle
NexPage idlePage(1, 0, "idle");
NexButton idle_bHeatUp(1, 3, "bHeatUp");
NexButton idle_bSettings(1, 4, "bSettings");
//Page 2: heatup
NexPage heatupPage(2, 0, "heatup");
NexButton heatup_bCooldown(2, 2, "bCooldown");
NexButton heatup_bStartExt(2, 13, "bStartExt");
NexText heatup_tReady(2, 15, "tReady");
NexButton heatup_bTempMinus5(2, 8, "bTempMinus5");
NexButton heatup_bTempMinus1(2, 10, "bTempMinus1");
NexButton heatup_bTempPlus1(2, 11, "bTempPlus1");
NexButton heatup_bTempPlus5(2, 9, "bTempPlus5");
NexNumber heatup_nNominalTemp(2, 16, "nNominalTemp");
NexNumber heatup_nActualTemp(2, 4, "nActualTemp");
NexProgressBar heatup_jTempBar(2, 3, "jTempBar");
//Page 3: extrude
NexPage extrudePage(3, 0, "extrude");
NexButton extrude_bCooldown(3, 2, "bCooldown");
NexButton extrude_bPauseExt(3, 11, "bPauseExt");
NexButton extrude_bStartWind(3, 10, "bStartWind");
NexButton extrude_bTempMinus1(3, 8, "bTempMinus1");
NexButton extrude_bTempPlus1(3, 9, "bTempPlus1");
NexNumber extrude_nNominalTemp(3, 14, "nNominalTemp");
NexNumber extrude_nActualTemp(3, 4, "nActualTemp");
NexProgressBar extrude_jTempBar(3, 3, "jTempBar");
//Page 4: windup
NexPage windupPage(4, 0, "windup");
NexButton windup_bCooldown(4, 2, "bCooldown");
NexButton windup_bPauseWind(4, 10, "bPauseWind");
NexButton windup_bTempMinus1(4, 8, "bTempMinus1");
NexButton windup_bTempPlus1(4, 9, "bTempPlus1");
NexButton windup_bSpeedMin01(4, 14, "bSpeedMin01");
NexButton windup_bSpeedMin001(4, 15, "bSpeedMin001");
NexButton windup_bSpeedPlus01(4, 12, "bSpeedPlus01");
NexButton windup_bSpeedPlus001(4, 13, "bSpeedPlus001");
NexNumber windup_nNominalTemp(4, 10, "nNominalTemp");
NexText windup_tSpeed(4, 16, "tSpeed");
NexNumber windup_nActualTemp(4, 4, "nActualTemp");
NexProgressBar windup_jTempBar(4, 3, "jTempBar");
//Page 5: settings
NexPage settingsPage(5, 0, "settings");
NexButton settings_bSave(5, 27, "bSave");
NexButton settings_bTempMinus5(5, 2, "bTempMinus5");
NexButton settings_bTempMinus1(5, 4, "bTempMinus1");
NexButton settings_bTempPlus1(5, 5, "bTempPlus1");
NexButton settings_bTempPlus5(5, 3, "bTempPlus5");
NexButton settings_bWidthMinus5(5, 29, "bWidthMinus5");
NexButton settings_bWidthMinus1(5, 30, "bWidthMinus1");
NexButton settings_bWidthPlus1(5, 32, "bWidthPlus1");
NexButton settings_bWidthPlus5(5, 33, "bWidthPlus5");
NexButton settings_bPickupMinus5(5, 9, "bPickupMinus5");
NexButton settings_bPickupMinus1(5, 11, "bPickupMinus1");
NexButton settings_bPickupPlus1(5, 12, "bPickupPlus1");
NexButton settings_bPickupPlus5(5, 10, "bPickupPlus5");
NexButton settings_bInnerMinus5(5, 21, "bInnerMinus5");
NexButton settings_bInnerMinus1(5, 23, "bInnerMinus1");
NexButton settings_bInnerPlus1(5, 24, "bInnerPlus1");
NexButton settings_bInnerPlus5(5, 22, "bInnerPlus5");
NexButton settings_bOuterMinus5(5, 27, "bOuterMinus5");
NexButton settings_bOuterMinus1(5, 29, "bOuterMinus1");
NexButton settings_bOuterPlus1(5, 30, "bOuterPlus1");
NexButton settings_bOuterPlus5(5, 28, "bOuterPlus5");
NexNumber settings_nTemp(5, 7, "nTemp");
NexText settings_tPickup(5, 14, "tPickup");
NexText settings_tWidth(5, 20, "tWidth");
NexText settings_tInnerDia(5, 26, "tInnerDia");
NexText settings_tOuterDia(5, 32, "tOuterDia");

//Create touch event list
NexTouch *nexListenList[] = {
  //Page 1: idle
  &idle_bHeatUp,
  &idle_bSettings,
  //Page 2: heatup
  &heatup_bCooldown,
  &heatup_bStartExt,
  &heatup_tReady,
  &heatup_bTempMinus5,
  &heatup_bTempMinus1,
  &heatup_bTempPlus1,
  &heatup_bTempPlus5,
  //Page 3: extrude
  &extrude_bCooldown,
  &extrude_bPauseExt,
  &extrude_bStartWind,
  &extrude_bTempMinus1,
  &extrude_bTempPlus1,
  //Page 4: windup
  &windup_bCooldown,
  &windup_bPauseWind,
  &windup_bTempMinus1,
  &windup_bTempPlus1,
  &windup_bSpeedMin01,
  &windup_bSpeedMin001,
  &windup_bSpeedPlus01,
  &windup_bSpeedPlus001,
  //Page 5: settings
  &settings_bSave,
  &settings_bTempMinus5,
  &settings_bTempMinus1,
  &settings_bTempPlus1,
  &settings_bTempPlus5,
  &settings_bWidthMinus5,
  &settings_bWidthMinus1,
  &settings_bWidthPlus1,
  &settings_bWidthPlus5,
  &settings_bPickupMinus5,
  &settings_bPickupMinus1,
  &settings_bPickupPlus1,
  &settings_bPickupPlus5,
  &settings_bInnerMinus5,
  &settings_bInnerMinus1,
  &settings_bInnerPlus1,
  &settings_bInnerPlus5,
  &settings_bOuterMinus5,
  &settings_bOuterMinus1,
  &settings_bOuterPlus1,
  &settings_bOuterPlus5,
  NULL
};

//Define button callback functions
//Page 1: idle
void idle_bHeatup_callback() {
  heatupPage.show();
  currentState = heatup;
  heatup_nNominalTemp.setValue((int)nominalTemp);
  heatup_nActualTemp.setValue((int)actualTemp);
  dbSerialPrintln("currentState = heatup");
}
void idle_bSettings_callback() {
  settingsPage.show();
  currentState = settings;
  settings_nTemp.setValue((int)nominalTemp);
  settings_tWidth.setText(String(spoolWidth) + "mm");
  settings_tPickup.setText(String(spoolPickupDiameter) + "mm");
  settings_tInnerDia.setText(String(spoolInnerDiameter) + "mm");
  settings_tOuterDia.setText(String(spoolOuterDiameter) + "mm");
  dbSerialPrintln("currentState = settings");
}
//Page 2: heatup
void heatup_bCooldown_callback() {
  idlePage.show();
  currentState = idle;
  analogWrite(HEATER_1, 0);
  analogWrite(HEATER_2, 0);
  analogWrite(HEATER_3, 0);
  dbSerialPrintln("currentState = idle");
}
void heatup_bStartExt_callback() {
  extrudePage.show();
  currentState = extrude;
  extrude_nNominalTemp.setValue((int)nominalTemp);
  extrude_nActualTemp.setValue((int)actualTemp);
  digitalWrite(EXTRUDER_MOTOR, HIGH);
  dbSerialPrintln("currentState = extrude");
}
void heatup_bTempMinus5_callback() {
  nominalTemp -= 5;
  heatup_nNominalTemp.setValue((int)nominalTemp);
}
void heatup_bTempMinus1_callback() {
  nominalTemp -= 1;
  heatup_nNominalTemp.setValue((int)nominalTemp);
}
void heatup_bTempPlus1_callback() {
  nominalTemp += 1;
  heatup_nNominalTemp.setValue((int)nominalTemp);
}
void heatup_bTempPlus5_callback() {
  nominalTemp += 5;
  heatup_nNominalTemp.setValue((int)nominalTemp);
}
//Page 3: extrude
void extrude_bCooldown_callback() {
  idlePage.show();
  currentState = idle;
  digitalWrite(EXTRUDER_MOTOR, LOW);
  analogWrite(HEATER_1, 0);
  analogWrite(HEATER_2, 0);
  analogWrite(HEATER_3, 0);
  dbSerialPrintln("currentState = idle");
}
void extrude_bPauseExt_callback() {
  heatupPage.show();
  currentState = heatup;
  digitalWrite(EXTRUDER_MOTOR, LOW);
  heatup_nNominalTemp.setValue((int)nominalTemp);
  heatup_nActualTemp.setValue((int)actualTemp);
  dbSerialPrintln("currentState = heatup");
}
void extrude_bStartWind_callback() {
  windupPage.show();
  startWindup();
  currentState = windup;
  windup_tSpeed.setText(String(windupSpeed).substring(0, 4) + " RPM");
  windup_nNominalTemp.setValue((int)nominalTemp);
  windup_nActualTemp.setValue((int)actualTemp);
  dbSerialPrintln("currentState = windup");
}
void extrude_bTempMinus1_callback() {
  nominalTemp -= 1;
  extrude_nNominalTemp.setValue((int)nominalTemp);
}
void extrude_bTempPlus1_callback() {
  nominalTemp += 1;
  extrude_nNominalTemp.setValue((int)nominalTemp);
}
//Page 4: windup
void windup_bCooldown_callback() {
  idlePage.show();
  stopWindup();
  currentState = idle;
  digitalWrite(EXTRUDER_MOTOR, LOW);
  analogWrite(HEATER_1, 0);
  analogWrite(HEATER_2, 0);
  analogWrite(HEATER_3, 0);
  dbSerialPrintln("currentState = idle");
}
void windup_bPauseWind_callback() {
  extrudePage.show();
  stopWindup();
  currentState = extrude;
  extrude_nNominalTemp.setValue((int)nominalTemp);
  extrude_nActualTemp.setValue((int)actualTemp);
  dbSerialPrintln("currentState = extrude");
}
void windup_bTempMinus1_callback() {
  nominalTemp -= 1;
  windup_nNominalTemp.setValue((int)nominalTemp);
}
void windup_bTempPlus1_callback() {
  nominalTemp += 1;
  windup_nNominalTemp.setValue((int)nominalTemp);
}
void windup_bSpeedMin01_callback() {
  speedOffset -= 10;
  startWindup();
}
void windup_bSpeedMin001_callback() {
  speedOffset -= 1;
  startWindup();
}
void windup_bSpeedPlus01_callback() {
  speedOffset += 10;
  startWindup();
}
void windup_bSpeedPlus001_callback() {
  speedOffset += 1;
  startWindup();
}
//Page 5: settings
void settings_bSave_callback() {
  idlePage.show();
  currentState = idle;
  dbSerialPrintln("currentState = idle");
}
void settings_bTempMinus5_callback() {
  nominalTemp -= 5;
  settings_nTemp.setValue((int)nominalTemp);
}
void settings_bTempMinus1_callback() {
  nominalTemp -= 1;
  settings_nTemp.setValue((int)nominalTemp);
}
void settings_bTempPlus1_callback() {
  nominalTemp += 1;
  settings_nTemp.setValue((int)nominalTemp);
}
void settings_bTempPlus5_callback() {
  nominalTemp += 5;
  settings_nTemp.setValue((int)nominalTemp);
}
void settings_bWidthMinus5_callback() {
  spoolWidth -= 5;
  settings_tWidth.setText(String(spoolWidth) + "mm");
}
void settings_bWidthMinus1_callback() {
  spoolWidth -= 1;
  settings_tWidth.setText(String(spoolWidth) + "mm");
}
void settings_bWidthPlus1_callback() {
  spoolWidth += 1;
  settings_tWidth.setText(String(spoolWidth) + "mm");
}
void settings_bWidthPlus5_callback() {
  spoolWidth += 5;
  settings_tWidth.setText(String(spoolWidth) + "mm");
}
void settings_bPickupMinus5_callback() {
  spoolPickupDiameter -= 5;
  settings_tPickup.setText(String(spoolPickupDiameter) + "mm");
}
void settings_bPickupMinus1_callback() {
  spoolPickupDiameter -= 1;
  settings_tPickup.setText(String(spoolPickupDiameter) + "mm");
}
void settings_bPickupPlus1_callback() {
  spoolPickupDiameter += 1;
  settings_tPickup.setText(String(spoolPickupDiameter) + "mm");
}
void settings_bPickupPlus5_callback() {
  spoolPickupDiameter += 5;
  settings_tPickup.setText(String(spoolPickupDiameter) + "mm");
}
void settings_bInnerMinus5_callback() {
  spoolInnerDiameter -= 5;
  settings_tInnerDia.setText(String(spoolInnerDiameter) + "mm");
}
void settings_bInnerMinus1_callback() {
  spoolInnerDiameter -= 1;
  settings_tInnerDia.setText(String(spoolInnerDiameter) + "mm");
}
void settings_bInnerPlus1_callback() {
  spoolInnerDiameter += 1;
  settings_tInnerDia.setText(String(spoolInnerDiameter) + "mm");
}
void settings_bInnerPlus5_callback() {
  spoolInnerDiameter += 5;
  settings_tInnerDia.setText(String(spoolInnerDiameter) + "mm");
}
void settings_bOuterMinus5_callback() {
  spoolOuterDiameter -= 5;
  settings_tOuterDia.setText(String(spoolOuterDiameter) + "mm");
}
void settings_bOuterMinus1_callback() {
  spoolOuterDiameter -= 1;
  settings_tOuterDia.setText(String(spoolOuterDiameter) + "mm");
}
void settings_bOuterPlus1_callback() {
  spoolOuterDiameter += 1;
  settings_tOuterDia.setText(String(spoolOuterDiameter) + "mm");
}
void settings_bOuterPlus5_callback() {
  spoolOuterDiameter += 5;
  settings_tOuterDia.setText(String(spoolOuterDiameter) + "mm");
}

//Define init functions
void initSensors() {
  pt100.begin(MAX31865_2WIRE);
}
void initPID() {
  pinMode(HEATER_1, OUTPUT);
  pinMode(HEATER_2, OUTPUT);
  pinMode(HEATER_3, OUTPUT);
  pid.SetMode(AUTOMATIC);
}
void initExtruderMotor() {
  pinMode(EXTRUDER_MOTOR, OUTPUT);
}
void initWindup() {
  pinMode(INIT_SIGNAL, INPUT);
  pinMode(REF_SIGNAL, INPUT);
  pinMode(WINDUP_SIGNAL, OUTPUT);
}

//Define windup functions
void startWindup() {
  //String architecture: "SPOOL_WIDTH;SPOOL_PICKUP_DIAMETER;SPOOL_INNER_DIAMETER;SPOOL_OUTER_DIAMETER;"
  Serial1.print(String(spoolWidth) + ";"); 
  Serial1.print(String(spoolPickupDiameter) + ";");
  Serial1.print(String(spoolInnerDiameter) + ";");
  Serial1.print(String(spoolOuterDiameter) + ";");
  Serial1.print(String(speedOffset) + ";");
  delay(100);
  digitalWrite(WINDUP_SIGNAL, HIGH);
}
void stopWindup() {
  digitalWrite(WINDUP_SIGNAL, LOW);
}

//Define state machine evaluations
void evalStates() {
  switch(currentState) {
    case initialize:
      dbSerialPrintln("currentState = init");
      initPage.show();
      initSensors();
      init_pInitSensors.show();
      initPID();
      init_pInitPID.show();
      initExtruderMotor();
      initWindup();
      while(digitalRead(INIT_SIGNAL) == LOW) {}
      init_pInitMotors.show();
      currentState = refStep;
      dbSerialPrintln("currentState = refStep");
      break;
    case refStep:
      while(digitalRead(REF_SIGNAL) == LOW) {}
      init_pRefStepper.show();
      delay(500);
      idlePage.show();
      currentState = idle;
      dbSerialPrintln("currentState = idle");
      break;
    case idle:
      break;
    case settings:
      break;
    case heatup:
      actualTemp = pt100.temperature(RNOMINAL, RREF);
      if(millis() >= updateTime + UPDATE_INTERVAL) {
        heatup_nActualTemp.setValue((int)actualTemp);
        heatup_jTempBar.setValue(actualTemp / nominalTemp * 100);
        updateTime = millis();
      }
      pid.Compute();
      analogWrite(HEATER_1, heaterOutput);
      analogWrite(HEATER_2, heaterOutput);
      analogWrite(HEATER_3, heaterOutput);
      if(actualTemp >= nominalTemp - ALLOWED_TEMP_DEVIATION && actualTemp <= nominalTemp + ALLOWED_TEMP_DEVIATION) {
        heatup_bStartExt.show();
        heatup_tReady.show();
        currentState = ready;
        dbSerialPrintln("currentState = ready");
      }
      break;
    case ready:
      actualTemp = pt100.temperature(RNOMINAL, RREF);
      if(millis() >= updateTime + UPDATE_INTERVAL) {
        heatup_nActualTemp.setValue((int)actualTemp);
        heatup_jTempBar.setValue(actualTemp / nominalTemp * 100);
        updateTime = millis();
      }
      pid.Compute();
      analogWrite(HEATER_1, heaterOutput);
      analogWrite(HEATER_2, heaterOutput);
      analogWrite(HEATER_3, heaterOutput);
      if(actualTemp > nominalTemp + ALLOWED_TEMP_DEVIATION || actualTemp < nominalTemp - ALLOWED_TEMP_DEVIATION) {
        heatup_bStartExt.hide();
        heatup_tReady.hide();
        currentState = heatup;
        heatup_nNominalTemp.setValue((int)nominalTemp);
        heatup_nActualTemp.setValue((int)actualTemp);
        dbSerialPrintln("currentState = heatup");
      }
      break;
    case extrude:
      actualTemp = pt100.temperature(RNOMINAL, RREF);
      if(millis() >= updateTime + UPDATE_INTERVAL) {
        extrude_nActualTemp.setValue((int)actualTemp);
        extrude_jTempBar.setValue(actualTemp / nominalTemp * 100);
        updateTime = millis();
      }
      pid.Compute();
      analogWrite(HEATER_1, heaterOutput);
      analogWrite(HEATER_2, heaterOutput);
      analogWrite(HEATER_3, heaterOutput);
      if(actualTemp > nominalTemp + ALLOWED_TEMP_DEVIATION || actualTemp < nominalTemp - ALLOWED_TEMP_DEVIATION) {
        heatup_bStartExt.hide();
        heatup_tReady.hide();
        currentState = heatup;
        digitalWrite(EXTRUDER_MOTOR, LOW);
        heatup_nNominalTemp.setValue((int)nominalTemp);
        heatup_nActualTemp.setValue((int)actualTemp);
        dbSerialPrintln("currentState = heatup");
      }
      break;
    case windup:
      actualTemp = pt100.temperature(RNOMINAL, RREF);
      if(millis() >= updateTime + UPDATE_INTERVAL) {
        windup_nActualTemp.setValue((int)actualTemp);
        windup_jTempBar.setValue(actualTemp / nominalTemp * 100);
        updateTime = millis();
      }
      pid.Compute();
      analogWrite(HEATER_1, heaterOutput);
      analogWrite(HEATER_2, heaterOutput);
      analogWrite(HEATER_3, heaterOutput);
      if(Serial1.available()) {
        windupSpeed = Serial1.readStringUntil(';').toFloat();
        windup_tSpeed.setText(String(windupSpeed).substring(0, 4) + " RPM");
      }
      if(actualTemp > nominalTemp + ALLOWED_TEMP_DEVIATION || actualTemp < nominalTemp - ALLOWED_TEMP_DEVIATION) {
        heatup_bStartExt.hide();
        heatup_tReady.hide();
        stopWindup();
        currentState = heatup;
        digitalWrite(EXTRUDER_MOTOR, LOW);
        heatup_nNominalTemp.setValue((int)nominalTemp);
        heatup_nActualTemp.setValue((int)actualTemp);
        dbSerialPrintln("currentState = heatup");
      }
      break;
    default:
      break;
  }
}

void setup() {
  //Initialize display
  nexInit();

  //Open debug serial 
  Serial.begin(9600);

  //Open windup serial
  Serial1.begin(9600);

  //Register callback functions
  //Page 1: idle
  idle_bHeatUp.attachPop(idle_bHeatup_callback);
  idle_bSettings.attachPop(idle_bSettings_callback);
  //Page 2: heatup
  heatup_bCooldown.attachPop(heatup_bCooldown_callback);
  heatup_bStartExt.attachPop(heatup_bStartExt_callback);
  heatup_bTempMinus5.attachPop(heatup_bTempMinus5_callback);
  heatup_bTempMinus1.attachPop(heatup_bTempMinus1_callback);
  heatup_bTempPlus1.attachPop(heatup_bTempPlus1_callback);
  heatup_bTempPlus5.attachPop(heatup_bTempPlus5_callback);
  //Page 3: extrude
  extrude_bCooldown.attachPop(extrude_bCooldown_callback);
  extrude_bPauseExt.attachPop(extrude_bPauseExt_callback);
  extrude_bStartWind.attachPop(extrude_bStartWind_callback);
  extrude_bTempMinus1.attachPop(extrude_bTempMinus1_callback);
  extrude_bTempPlus1.attachPop(extrude_bTempPlus1_callback);
  //Page 4: windup
  windup_bCooldown.attachPop(windup_bCooldown_callback);
  windup_bPauseWind.attachPop(windup_bPauseWind_callback);
  windup_bTempMinus1.attachPop(windup_bTempMinus1_callback);
  windup_bTempPlus1.attachPop(windup_bTempPlus1_callback);
  windup_bSpeedMin01.attachPop(windup_bSpeedMin01_callback);
  windup_bSpeedMin001.attachPop(windup_bSpeedMin001_callback);
  windup_bSpeedPlus01.attachPop(windup_bSpeedPlus01_callback);
  windup_bSpeedPlus001.attachPop(windup_bSpeedPlus001_callback);
  //Page 5: settings
  settings_bSave.attachPop(settings_bSave_callback);
  settings_bTempMinus5.attachPop(settings_bTempMinus5_callback);
  settings_bTempMinus1.attachPop(settings_bTempMinus1_callback);
  settings_bTempPlus1.attachPop(settings_bTempPlus1_callback);
  settings_bTempPlus5.attachPop(settings_bTempPlus5_callback);
  settings_bWidthMinus5.attachPop(settings_bWidthMinus5_callback);
  settings_bWidthMinus1.attachPop(settings_bWidthMinus1_callback);
  settings_bWidthPlus1.attachPop(settings_bWidthPlus1_callback);
  settings_bWidthPlus5.attachPop(settings_bWidthPlus5_callback);
  settings_bPickupMinus5.attachPop(settings_bPickupMinus5_callback);
  settings_bInnerMinus5.attachPop(settings_bInnerMinus5_callback);
  settings_bInnerMinus1.attachPop(settings_bInnerMinus1_callback);
  settings_bInnerPlus1.attachPop(settings_bInnerPlus1_callback);
  settings_bInnerPlus5.attachPop(settings_bInnerPlus5_callback);
  settings_bOuterMinus5.attachPop(settings_bOuterMinus5_callback);
  settings_bOuterMinus1.attachPop(settings_bOuterMinus1_callback);
  settings_bOuterPlus1.attachPop(settings_bOuterPlus1_callback);
  settings_bOuterPlus5.attachPop(settings_bOuterPlus5_callback);
}

void loop() {
  evalStates();
  nexLoop(nexListenList);
}

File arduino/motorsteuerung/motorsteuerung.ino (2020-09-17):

#include <AccelStepper.h>

//Define defaults
#define SPOOL_WIDTH 73 //[mm]
#define SPOOL_PICKUP_DIAMETER 53 //[mm]
#define SPOOL_INNER_DIAMETER 100 //[mm]
#define SPOOL_OUTER_DIAMETER 200 //[mm]
#define SPOOL_SIDE_THICKNESS 3.5 //[mm]

//Define other process parameters
#define EXTRUSION_FEED 7.0 //[mm/s]
#define FILAMENT_DIAMETER 1.75 //[mm]
#define M12_PITCH 1.75 //[mm]
#define STEPS_PER_REVOLUTION 6400L //[steps]
#define MAX_GUIDE_POS 77 //[mm]
#define SETUP_MIN_MSG_LENGTH 14 //[bytes]

//Define stepper motor pins
#define STEPPER_SPOOL_STP 10 //Any digital pin 
#define STEPPER_SPOOL_DIR 9 //Any digital pin 
#define STEPPER_GUIDE_STP 12 //Any digital pin 
#define STEPPER_GUIDE_DIR 11 //Any digital pin 

//Define endstop pin 
#define ENDSTOP 13 //Any digital pin

//Define signal pins 
#define INIT_SIGNAL 5 //Any digital pin 
#define REF_SIGNAL 6 //Any digital pin 
#define WINDUP_SIGNAL 7 //Any digital pin 

//Declare extruder process variables
int spoolWidth = SPOOL_WIDTH; 
int spoolPickupDiameter = SPOOL_PICKUP_DIAMETER;
int spoolInnerDiameter = SPOOL_INNER_DIAMETER;
int spoolOuterDiameter = SPOOL_OUTER_DIAMETER;
float endstopOffset = tan(0.87266) * (65 - spoolPickupDiameter) / 2 - 1.3 + SPOOL_SIDE_THICKNESS; //[mm]
long endstopOffsetSteps = endstopOffset / M12_PITCH * STEPS_PER_REVOLUTION; //[steps]
int speedOffset = 0;

//Declare stepper motors and corresponding variables
AccelStepper stepperSpool(1, STEPPER_SPOOL_STP, STEPPER_SPOOL_DIR);
AccelStepper stepperGuide(1, STEPPER_GUIDE_STP, STEPPER_GUIDE_DIR);
double windupSpeed = 0.0; //[1/min]
int turnsPerLayer = 0;
int stepsPerSecond = 0; //[1/s]
int currentLayer = -1;

void initMotors() {
  pinMode(STEPPER_SPOOL_STP, OUTPUT);
  pinMode(STEPPER_SPOOL_DIR, OUTPUT);
  pinMode(STEPPER_GUIDE_STP, OUTPUT); 
  pinMode(STEPPER_GUIDE_DIR, OUTPUT);
  stepperSpool.setMaxSpeed(10000); //[steps/s]
  stepperGuide.setMaxSpeed(10000); //[steps/s]
  windupSpeed = EXTRUSION_FEED / (SPOOL_INNER_DIAMETER * M_PI) * 60; //[1/min]
  stepsPerSecond = windupSpeed / 60 * STEPS_PER_REVOLUTION; //[1/s]
  stepperSpool.setCurrentPosition(0); //[steps]
}

void refStep() {
  stepperGuide.setSpeed(10000); //[steps/s]
  while(digitalRead(ENDSTOP) == LOW) {
    stepperGuide.runSpeed();
  }
  stepperGuide.setCurrentPosition(0); //[steps]
  stepperGuide.moveTo(- endstopOffsetSteps); //[steps]
  stepperGuide.setSpeed(-5000); //[steps/s]
  while(stepperGuide.currentPosition() != stepperGuide.targetPosition()) {
    stepperGuide.runSpeed();
  }
}

void calculateSpeed() {
  turnsPerLayer = (((spoolWidth + endstopOffset) > MAX_GUIDE_POS ? MAX_GUIDE_POS - endstopOffset : spoolWidth) - 2 * SPOOL_SIDE_THICKNESS) / FILAMENT_DIAMETER;
  windupSpeed = EXTRUSION_FEED / ((spoolInnerDiameter + currentLayer * 2 * FILAMENT_DIAMETER) * M_PI) * 60; //[1/min]
  windupSpeed = windupSpeed + (speedOffset / 100.0);
  stepsPerSecond = windupSpeed / 60 * STEPS_PER_REVOLUTION; //[1/s]
  stepperGuide.setSpeed(stepperGuide.speed() < 0 ? -stepsPerSecond : stepsPerSecond);
  stepperSpool.setSpeed(stepsPerSecond); 
  Serial.print(String(windupSpeed) + ";");
}

void windup() {
  if(stepperGuide.currentPosition() != stepperGuide.targetPosition()) {
    stepperGuide.runSpeed();
    stepperSpool.runSpeed();
  } else {
    currentLayer++;
    calculateSpeed();
    if(stepperGuide.currentPosition() == - endstopOffsetSteps) {
      stepperGuide.moveTo(- endstopOffsetSteps - (STEPS_PER_REVOLUTION * turnsPerLayer + FILAMENT_DIAMETER / 2));
      stepperGuide.setSpeed(- stepsPerSecond);
    } else {
      stepperGuide.moveTo(- endstopOffsetSteps);
      stepperGuide.setSpeed(stepsPerSecond);
    }
    stepperGuide.runSpeed();
    stepperSpool.moveTo(stepperSpool.currentPosition() + STEPS_PER_REVOLUTION * turnsPerLayer);
    stepperSpool.setSpeed(stepsPerSecond);
    stepperSpool.runSpeed();
  }
}

void setup() {
  Serial.begin(9600);
  pinMode(ENDSTOP, INPUT);
  pinMode(INIT_SIGNAL, OUTPUT);
  pinMode(REF_SIGNAL, OUTPUT);
  pinMode(WINDUP_SIGNAL, INPUT);
  initMotors();
  digitalWrite(INIT_SIGNAL, HIGH);
  refStep();
  digitalWrite(REF_SIGNAL, HIGH);
  delay(100);
  digitalWrite(INIT_SIGNAL, LOW);
  digitalWrite(REF_SIGNAL, LOW);
}

void loop() {
  if(Serial.available() >= SETUP_MIN_MSG_LENGTH) {
    //String architecture: "SPOOL_WIDTH;SPOOL_PICKUP_DIAMETER;SPOOL_INNER_DIAMETER;SPOOL_OUTER_DIAMETER;SPEED_OFFSET;"
    spoolWidth = Serial.readStringUntil(';').toInt(); 
    spoolPickupDiameter = Serial.readStringUntil(';').toInt();
    spoolInnerDiameter = Serial.readStringUntil(';').toInt();
    spoolOuterDiameter = Serial.readStringUntil(';').toInt();
    speedOffset = Serial.readStringUntil(';').toInt();
    endstopOffset = tan(0.87266) * (65 - spoolPickupDiameter) / 2 - 1.3 + SPOOL_SIDE_THICKNESS; //[mm]
    endstopOffsetSteps = endstopOffset / M12_PITCH * STEPS_PER_REVOLUTION; //[steps]
    calculateSpeed();
  }
  if(digitalRead(WINDUP_SIGNAL) == HIGH) {
    windup();
  }
}

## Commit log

2020-08-12 finished display prototype
2020-08-12 fixed text conversion and serial config
    [filamentextruder.ino]
2020-08-14 Final HMI prototype
2020-08-14 Add extruder.HMI
2020-08-19 Implement PT100 and PID
    [basis.stl, führung.stl, lageraufnahme.stl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]
2020-08-19 Implement stepper motors
2020-09-17 Complete arduino code
2020-09-17 Adjust extrusion feed
    [fuehrung_v2.stl, führung.stl]
2020-09-24 Add wiring scheme
2020-09-24 Update wiring scheme
2020-09-24 Add wiring description
2020-09-24 Add PID setup plots
2020-10-04 Update print files & README.md
    [führung_basis.stl, führung_positionierer.stl, führung_sensorhalter.stl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]
